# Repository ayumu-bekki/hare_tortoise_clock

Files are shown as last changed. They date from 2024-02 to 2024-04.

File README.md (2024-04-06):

# ノウサギとリクガメの時計

ESP32でステッピングモーターを制御して直線上に時・分を示す壁掛け時計。
http://blog.bekki.jp/article/190781348.html
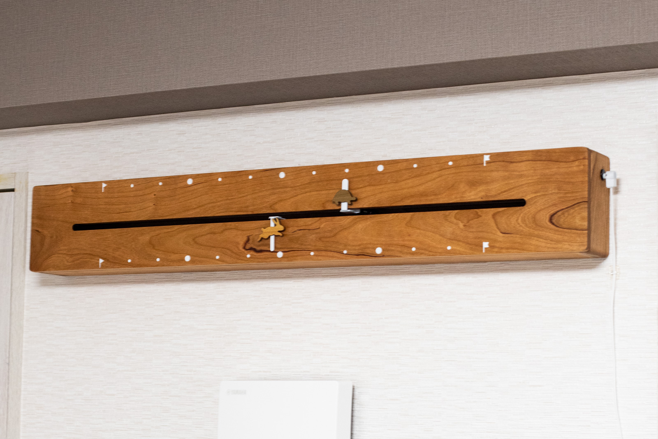
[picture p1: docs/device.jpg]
Device


## 設定方法

下記URLから時計の設定が可能。(対応環境:Bluetooth Low Energyに対応したマシン/iOS非対応 Chrome系ブラウザ)

[https://ayumu-bekki.github.io/hare_tortoise_clock/web_client/](https://ayumu-bekki.github.io/hare_tortoise_clock/web_client/)

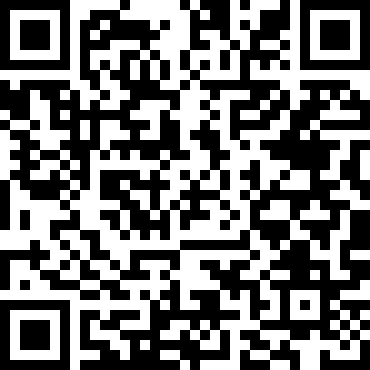
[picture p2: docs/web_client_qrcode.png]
Schematic


## ソフトウェア

* ESP-IDF v5.2 (https://docs.espressif.com/projects/esp-idf/en/latest/esp32/get-started/)

## ハードウェア

### 回路図

- メインマイコン
    - [ESP32-DevKitC V4ボード](https://docs.espressif.com/projects/esp-idf/en/stable/esp32/hw-reference/esp32/get-started-devkitc.html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) 
- ステッピングモータードライバー
    - AT2100 https://ja.aliexpress.com/item/1005002225468581.html
- マイクロスイッチ
    - OMRON スイッチ SS-5GL2
- ステッピングモーター
    - 17hs08 1004s https://ja.aliexpress.com/item/4001014382025.html

Schematic

### 機械設計図

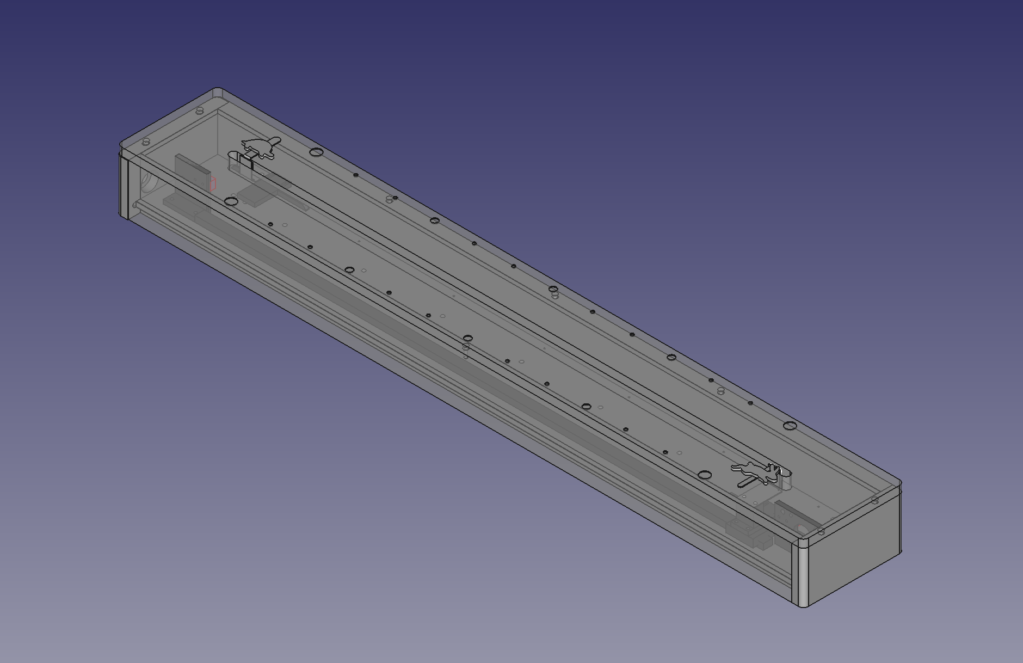
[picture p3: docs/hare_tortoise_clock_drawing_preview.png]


[図面(FreeCAD)](docs/hare_tortoise_clock_drawing.FCStd)

モーターブラケット・アイドラーブラケット・スライダーベースは、アルミニウム(A5052)削り出し

- スライドガイド
    - ミスミ スライドガイド SSEBZ-MX13-720
- アイドラー固定用軸 
    - ミスミ カタモチピンダンツキ SFXBA5A-9-F9
- プーリー・タイミングベルト
    - GT2 プーリー20mm ボア5mm 3Dプリンターキット https://ja.aliexpress.com/item/1005003025244723.html
    - ※上記商品だけではタイミングベルトの長さが足りないので別途入手が必要

### ステッカー

[本体貼付用(psd)](docs/hare_tortoise_clock_sticker.psd)

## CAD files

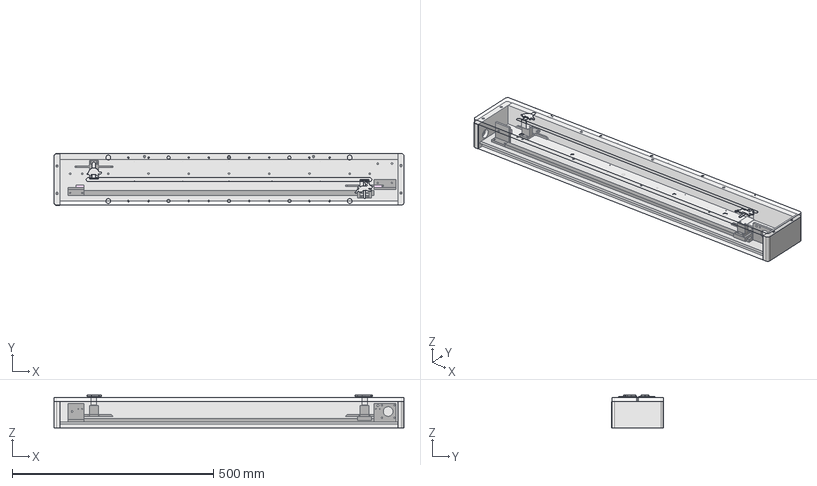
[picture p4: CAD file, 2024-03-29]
docs/hare_tortoise_clock_drawing.FCStd
870.0 x 129.0 x 81.0 mm
LinearGuide Rail
LinearGude Block
MotorMount
MicroSwitchMoter
IdlerMount
MicroSwitchIdler
SliderSolid
SliderSolidUp
BodyBack(Base)
BodyBottom
BodyRight
BodyFront
BodyLeft
BodyUp
MinuteHand
HourHand
MinuteAnimal
HourAnimal
HourLag
MinuteLag

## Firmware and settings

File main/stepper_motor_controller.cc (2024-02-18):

// ESP32 Hare Tortoise Clock
// (C)2024 bekki.jp

// Include ----------------------
#include "stepper_motor_controller.h"

#include <driver/gpio.h>
#include <driver/gptimer.h>
#include <esp_pthread.h>

#include <future>

#include "gpio_control.h"
#include "logger.h"
#include "message_queue.h"
#include "util.h"

namespace HareTortoiseClockSystem {

/// モータードライバーをON/OFFするインターバル時間(ms)
/// ステッピングモータードライバによって調整
constexpr int32_t ENABLE_INTERVAL = 20;
/// イベントキューサイズ
constexpr int32_t MOTOR_CONTROL_QUEUE_SIZE = 10;
/// イベントキュー最大待機tick
constexpr int32_t MOTOR_CONTROL_QUEUE_RECEIVE_LIMIT = 1000 / portTICK_PERIOD_MS;
/// 非同期実行時のスレッド名
constexpr std::string_view TASK_NAME = "StepperMotorTask";
/// 非同期実行時のスレッド利用CPUコア
constexpr int32_t CORE_ID = APP_CPU_NUM;

StepperMotorController::StepperMotorController(
    const uint32_t gptimer_resolution, const gpio_num_t gpio_enable,
    const gpio_num_t gpio_step, const gpio_num_t gpio_dir,
    const gpio_num_t gpio_right_limit, const gpio_num_t gpio_left_limit,
    const bool is_rotate_right_is_dir_up)
    : gptimer_resolution_(gptimer_resolution),
      gpio_enable_(gpio_enable),
      gpio_step_(gpio_step),
      gpio_dir_(gpio_dir),
      gpio_right_limit_(gpio_right_limit),
      gpio_left_limit_(gpio_left_limit),
      is_rotate_right_is_dir_up_(is_rotate_right_is_dir_up),
      motor_control_queue_(),
      gptimer_() {
  ESP_LOGI(TAG,
           "Initialize Stepper Motor ports > en:%d step:%d dir:%d "
           "right_limit:%d left_limit:%d",
           gpio_enable_, gpio_step_, gpio_dir_,
           gpio_right_limit_, gpio_left_limit_);

  // Init Gpio
  GPIO::InitOutput(gpio_enable_, 1);  // HIGHで無効 LOWで有効
  GPIO::InitOutput(gpio_step_, 0);
  GPIO::InitOutput(gpio_dir_, 0);  // HIGHで時計回り
  GPIO::InitInput(gpio_right_limit_);
  GPIO::InitInput(gpio_left_limit_);

  // Create MessageQueue
  if (!motor_control_queue_.Create(MOTOR_CONTROL_QUEUE_SIZE)) {
    ESP_LOGE(TAG, "Creating queue failed");
  }

  // Set Gpio Input Callback
  gpio_isr_handler_add(gpio_right_limit_,
                       &StepperMotorController::GpioRightLimitCallback,
                       &motor_control_queue_);
  gpio_isr_handler_add(gpio_left_limit_,
                       &StepperMotorController::GpioLeftLimitCallback,
                       &motor_control_queue_);

  // Create Timer
  gptimer_.Create(gptimer_resolution_, &StepperMotorController::TimerCallback,
                  &motor_control_queue_);
}

StepperMotorController::~StepperMotorController() {
  gptimer_.Destroy();

  motor_control_queue_.Destroy();

  gpio_isr_handler_remove(gpio_right_limit_);
  gpio_isr_handler_remove(gpio_left_limit_);

  GPIO::Reset(gpio_enable_);
  GPIO::Reset(gpio_step_);
  GPIO::Reset(gpio_dir_);
  GPIO::Reset(gpio_right_limit_);
  GPIO::Reset(gpio_left_limit_);
}

void StepperMotorController::EmergencyStop() {
  ESP_LOGI(TAG, "Stepper Motor. Add Queue EmergencyStop");
  motor_control_queue_.Send(EventType::EMERGENCY_STOP);
}

MoveResultFuture StepperMotorController::ExecMoveAsync(
    const StepperMotorExecInfo &exec_info) {
  // 新規スレッドを作る際の設定(コアを指定)
  esp_pthread_cfg_t cfg = esp_pthread_get_default_config();
  cfg.thread_name = std::string(TASK_NAME).c_str();
  cfg.pin_to_core = CORE_ID;
  esp_pthread_set_cfg(&cfg);

  return std::async(std::launch::async,
                    [this, exec_info] { return ExecMove(exec_info); });
}

MoveResult StepperMotorController::ExecMove(
    const StepperMotorExecInfo &exec_info) {
  ESP_LOGI(TAG, "Start Exec Motor. dir:%d step:%d", exec_info.dir_,
           exec_info.step_num_);
  // リミット事前チェック
  bool is_right_on = GPIO::GetLevel(gpio_right_limit_);
  bool is_left_on = GPIO::GetLevel(gpio_left_limit_);
  if (is_right_on && exec_info.dir_ == ROTATE_RIGHT) {
    ESP_LOGI(TAG, "Motor Limit Left");
    return RESULT_RIGHT_LIMIT;
  } else if (is_left_on && exec_info.dir_ == ROTATE_LEFT) {
    ESP_LOGI(TAG, "Motor Limit Right");
    return RESULT_LEFT_LIMIT;
  }

  // モーター動作
  int32_t record =
      exec_info.step_num_ *
      2;  // LOW/HIGHで1周期にするためループ回数を2倍にする(2回で1周期)
  EventType event_type = EventType::NONE;
  MoveResult result = RESULT_STEP_FINISH;

  GPIO::SetLevel(gpio_enable_, false);  // LOWで有効
  GPIO::SetLevel(gpio_step_, false);
  GPIO::SetLevel(gpio_dir_,  // HIGHで時計回り
                 !(is_rotate_right_is_dir_up_ ^ exec_info.dir_));
  Util::SleepMillisecond(ENABLE_INTERVAL);

  gptimer_.Start(exec_info.timer_tick_count_);

  while (record) {
    if (motor_control_queue_.ReceiveWait(&event_type,
                                         MOTOR_CONTROL_QUEUE_RECEIVE_LIMIT)) {
      if (event_type == EventType::TIMER) {
        record--;
        GPIO::SetLevel(gpio_step_, record % 2);
      } else if (event_type == EventType::INPUT_RIGHT_LIMIT) {
        is_right_on = GPIO::GetLevel(gpio_right_limit_);
        ESP_LOGD(TAG, "Right %s", is_right_on ? "ON" : "OFF");
        if (is_right_on && exec_info.dir_ == ROTATE_RIGHT) {
          result = RESULT_RIGHT_LIMIT;
          break;
        }
      } else if (event_type == EventType::INPUT_LEFT_LIMIT) {
        is_left_on = GPIO::GetLevel(gpio_left_limit_);
        ESP_LOGD(TAG, "Left %s", is_left_on ? "ON" : "OFF");
        if (is_left_on && exec_info.dir_ == ROTATE_LEFT) {
          result = RESULT_LEFT_LIMIT;
          break;
        }
      } else if (event_type == EventType::EMERGENCY_STOP) {
        result = RESULT_ERROR;
        break;
      }
    } else {
      ESP_LOGE(TAG, "Missed one count event");
      result = RESULT_ERROR;
      break;
    }
  }

  gptimer_.Stop();

  Util::SleepMillisecond(ENABLE_INTERVAL);
  GPIO::SetLevel(gpio_step_, false);
  GPIO::SetLevel(gpio_enable_, true);

  ESP_LOGI(TAG, "Finish Exec Motor");
  return result;
}

bool IRAM_ATTR StepperMotorController::TimerCallback(
    gptimer_handle_t timer, const gptimer_alarm_event_data_t *event_data,
    void *message_queue) {
  MessageQueue<EventType> *const queue =
      static_cast<MessageQueue<EventType> *>(message_queue);
  return queue->SendFromISR(EventType::TIMER);
}

void IRAM_ATTR
StepperMotorController::GpioLeftLimitCallback(void *message_queue) {
  MessageQueue<EventType> *const queue =
      static_cast<MessageQueue<EventType> *>(message_queue);
  queue->SendFromISR(EventType::INPUT_LEFT_LIMIT);
}

void IRAM_ATTR
StepperMotorController::GpioRightLimitCallback(void *message_queue) {
  MessageQueue<EventType> *const queue =
      static_cast<MessageQueue<EventType> *>(message_queue);
  queue->SendFromISR(EventType::INPUT_RIGHT_LIMIT);
}

}  // namespace HareTortoiseClockSystem

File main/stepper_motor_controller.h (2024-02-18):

#ifndef STEPPER_MOTOR_CONTROLLER_H_
#define STEPPER_MOTOR_CONTROLLER_H_
// ESP32 Hare Tortoise Clock
// (C)2024 bekki.jp

// Include ----------------------
#include <driver/gpio.h>
#include <driver/gptimer.h>
#include <soc/soc.h>

#include <chrono>
#include <future>
#include <memory>
#include <string_view>

#include "gptimer.h"
#include "message_queue.h"

namespace HareTortoiseClockSystem {

enum RotateDir {
  ROTATE_LEFT = 0,   // anti clockwise
  ROTATE_RIGHT = 1,  // clockwise
};

enum MoveResult {
  RESULT_NONE = 0,
  RESULT_STEP_FINISH = 1,
  RESULT_RIGHT_LIMIT = 2,
  RESULT_LEFT_LIMIT = 3,
  RESULT_ERROR = 4,
};

using MoveResultPromise = std::promise<MoveResult>;
using MoveResultFuture = std::future<MoveResult>;

/// ステッピングモーター実行情報
class StepperMotorExecInfo {
 public:
  StepperMotorExecInfo()
      : dir_(ROTATE_RIGHT), timer_tick_count_(0), step_num_(0) {}
  StepperMotorExecInfo(const RotateDir dir, const uint64_t timer_tick_count,
                       const int32_t step_num)
      : dir_(dir), timer_tick_count_(timer_tick_count), step_num_(step_num) {}

  const RotateDir dir_;
  const uint64_t timer_tick_count_;
  const int32_t step_num_;
};

/// ステッピングモーターコントロールクラス
class StepperMotorController {
 public:
  enum EventType {
    NONE = 0,
    TIMER = 1,
    INPUT_LEFT_LIMIT = 2,
    INPUT_RIGHT_LIMIT = 3,
    EMERGENCY_STOP = 4,
  };

 public:
  StepperMotorController(const uint32_t gptimer_resolution,
                         const gpio_num_t gpio_enable,
                         const gpio_num_t gpio_step, const gpio_num_t gpio_dir,
                         const gpio_num_t gpio_right_limit,
                         const gpio_num_t gpio_left_limit,
                         const bool is_rotate_right_is_dir_up);
  ~StepperMotorController();

  /// コピー禁止
  StepperMotorController(const StepperMotorController&) = delete;
  StepperMotorController& operator=(const StepperMotorController&) = delete;

  /// 緊急停止
  void EmergencyStop();

  /// モーター動作
  MoveResult ExecMove(const StepperMotorExecInfo& exec_info);
  /// モーター動作(非同期版)
  MoveResultFuture ExecMoveAsync(const StepperMotorExecInfo& exec_info);

 public:
  static bool TimerCallback(gptimer_handle_t timer,
                            const gptimer_alarm_event_data_t* event_data,
                            void* message_queue);
  static void GpioLeftLimitCallback(void* message_queue);
  static void GpioRightLimitCallback(void* message_queue);

 private:
  const uint32_t gptimer_resolution_;
  const gpio_num_t gpio_enable_;
  const gpio_num_t gpio_step_;
  const gpio_num_t gpio_dir_;
  const gpio_num_t gpio_right_limit_;
  const gpio_num_t gpio_left_limit_;
  const bool is_rotate_right_is_dir_up_;
  MessageQueue<EventType> motor_control_queue_;
  GPTimer gptimer_;
};

using StepperMotorControllerSharedPtr = std::shared_ptr<StepperMotorController>;
using StepperMotorControllerWeakPtr = std::weak_ptr<StepperMotorController>;

}  // namespace HareTortoiseClockSystem

#endif  // STEPPER_MOTOR_CONTROLLER_H_

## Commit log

2024-02-07 Git Version を自動的に組み込む対応
2024-02-07 時間合わせ時に緊急停止できない問題を修正
2024-02-07 sdksetting.oldを無視する対応
2024-02-08 ケースの設計図を更新
    [rabbit_clock_drawing.FCStd]
2024-02-08 READMEの更新
2024-02-08 READMEのリンク修正
2024-02-09 Webクライアントを修正
2024-02-09 StepperMotorTaskクラスの非同期周りを整備
2024-02-09 Queueを利用していた非同期処理をstd::futureに実装変更
2024-02-09 StepperMotorUtilの関数をconstexprに変更
2024-02-10 ドキュメント更新
2024-02-10 Github Pagesテスト
2024-02-10 Github Pages 公開用の仕組みを整備
2024-02-11 マイクロスイッチの位置が高かったため、図面をフィードバック
    [rabbit_clock_drawing.FCStd]
2024-02-11 Webクライアントの接続・切断周りの挙動を改善
2024-02-11 READMEにGithubPagesアドレスを追加
2024-02-12 ステッピングモーターコントローラーの改修
2024-02-12 回路図に誤りがあったため修正
2024-02-13 図面の修正(モーターブラケット側に配線用の穴を追加/秒針・時針の板金図面を追加)
    [rabbit_clock_drawing.FCStd, rabbit_clock_hands.FCStd]
2024-02-15 制御周りのコードを整理
2024-02-17 GPIOのデフォルト利用ポートと、回路図を変更
2024-02-17 GPIOポート番号の変更 回路図の修正 ステッピングモーターコントローラーの初期化時にGPIOポート番号をログ出力する対応を追加
2024-02-18 プロジェクト名変更とコード整理
    [hare_tortoise_clock_drawing.FCStd, hare_tortoise_clock_hands.FCStd, rabbit_clock_drawing.FCStd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]
2024-02-22 図面を統合し修正
    [hare_tortoise_clock_drawing.FCStd, hare_tortoise_clock_hands.FCStd]
2024-02-24 図面調整
    [hare_tortoise_clock_drawing.FCStd]
2024-03-03 文字盤用ステンシルデータ追加
2024-03-03 あられ組のサイズを6mm->10mmに変更
    [hare_tortoise_clock_drawing.FCStd]
2024-03-17 背面のキーホール位置が左右対称でなかったためフィードバック
    [hare_tortoise_clock_drawing.FCStd]
2024-03-18 MinuteHandの太さ・曲げ角を修正(対Meviey)
    [hare_tortoise_clock_drawing.FCStd]
2024-03-29 移動速度を抑えめに変更
2024-03-29 図面フィードバック
    [hare_tortoise_clock_drawing.FCStd]
2024-03-30 プレビュー画像を修正
2024-04-06 ドキュメント修正
